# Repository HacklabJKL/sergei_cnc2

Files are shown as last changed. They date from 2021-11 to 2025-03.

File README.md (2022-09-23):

Sergei 2 CNC machine project
============================

This repository contains design files for Hacklab Jyväskylä's CNC machine project.
The machine is built out of existing linear assemblies that have been donated to us, and as such it is not readily reproducible. But some of the modules may be useful and in any case this repository contains information for future maintenance of the machine.

The machine design is a compromise between router and mill designs.
In general router-type CNC machines are more useful for our typical projects, as they have larger work area for flat stock.
But in the same time it would be desirable for the machine to be sturdy enough to cut mild steel at reasonable speeds.

The basic design is similar to fixed gantry routers or a portal milling machine.
X axis ballscrew assembly moves up and down on two Z axis columns.
Y axis moves the table.

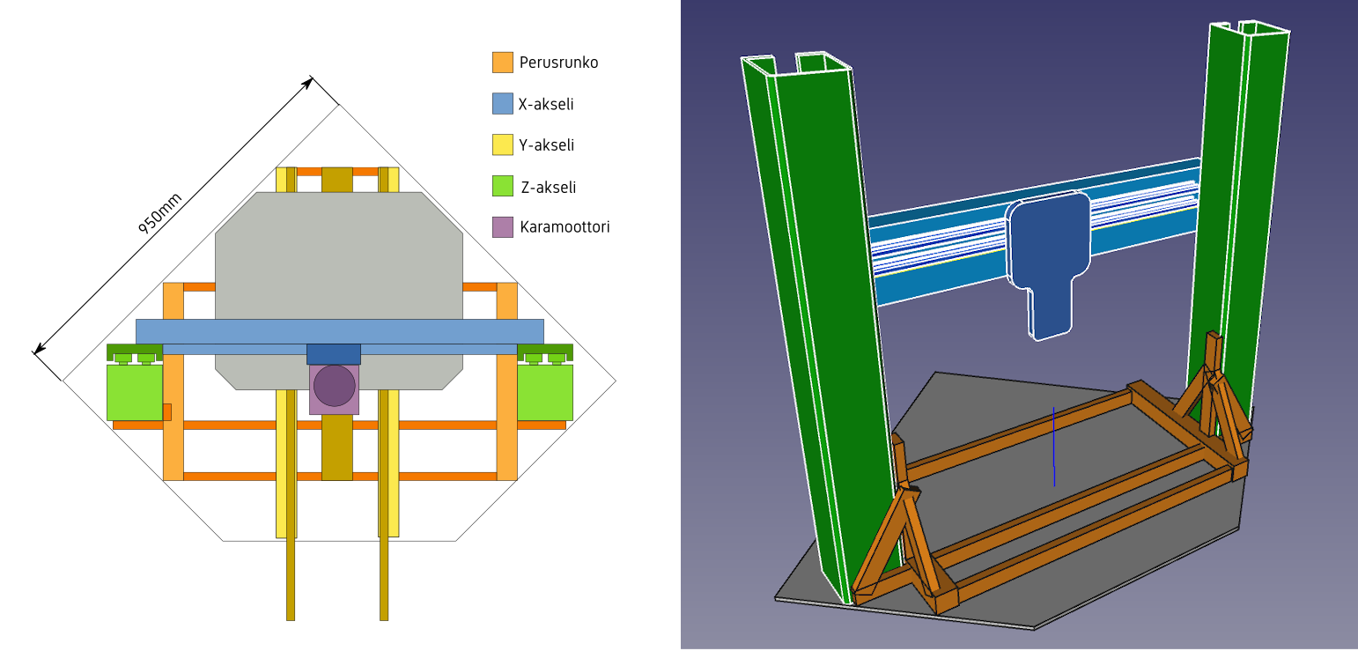
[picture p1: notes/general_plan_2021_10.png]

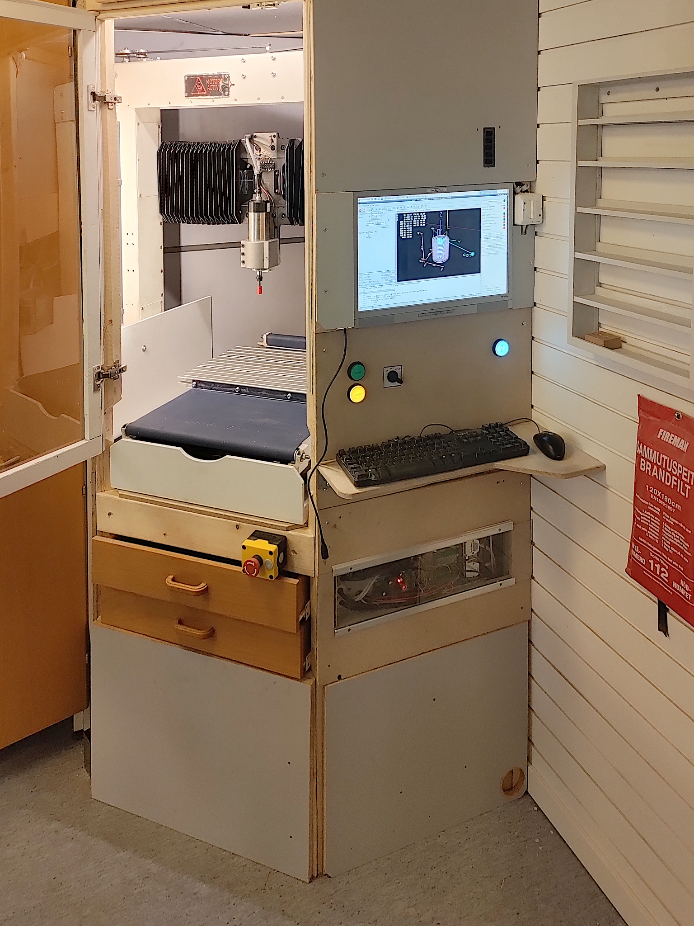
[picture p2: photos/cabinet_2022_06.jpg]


Documentation index
-------------------

* [Parts list](PARTS.md)
* [Wiring diagram](electronics/wiring/images/sergei2-wiring.pdf)
* [Usage instructions (wiki)](https://github.com/HacklabJKL/sergei_cnc2/wiki)

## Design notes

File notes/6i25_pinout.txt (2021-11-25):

2 ports of 17 IO pins each.

Port 1:
- 5 pins X: FWD/REV/FAULT/A/B
- 5 pins Y: FWD/REV/FAULT/A/B
- 5 pins Z: FWD/REV/FAULT/A/B
- HCURR output

Port 2:
- 5 pins A: FWD/REV/FAULT/A/B
- 2 pins 48V: ON/OK
- 1 pin SPINDLE_ON
- 1 pin TOOL_SENSOR
- 1 pin PROBE
- 3 pins X/Y/Z home

Port 1:
 1: X_FWD
 2: X_REV
 3: X_HOME
 4: X_A
 5: X_B
 6: Y_FWD
 7: Y_REV
 8: Y_HOME
 9: Y_A
10: Y_B
11: Z_FWD
12: Z_REV
13: Z_HOME
14: Z_A
15: Z_B
16: MOTOR_FAULT
17: MOTOR_HCURR

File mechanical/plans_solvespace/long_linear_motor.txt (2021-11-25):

2 pcs, 150 cm, 4x4 cm aluminum profile
table material?
Not quite long enough

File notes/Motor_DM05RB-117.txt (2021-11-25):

Specs: DC 24 V, 2000 RPM

12 cogging steps

DC resistance 5.5 ohms
Inductance 7 mH

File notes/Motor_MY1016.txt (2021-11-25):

Bought from eBay.
Rated 24V 300W 17A 2750 RPM.

DC Resistance 0.4 ohm
Inductance 0.5 mH

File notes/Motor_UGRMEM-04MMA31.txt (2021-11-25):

Speed testing:

10V:  600 RPM, 0.4 A
20V: 1340 RPM, 0.5 A
30V: 2110 RPM, 0.6 A
40V: 2890 RPM, 0.7 A
50V: 3660 RPM, 0.8 A

Kv constant 70 RPM/V
Kt constant 0.14 Nm/A

1 cm rise, 1:1 ratio:
=> 0.04 mm per pulse, 0.01 mm per encoder step
=> max speed 60 cm/sec
=> force with 5A drive is 440 N

Could use different ratio gearing, 1:2 or 1:4.

Mating connector: Molex 0003091032

DC resistance 5 ohms
Inductance 0.5 mH

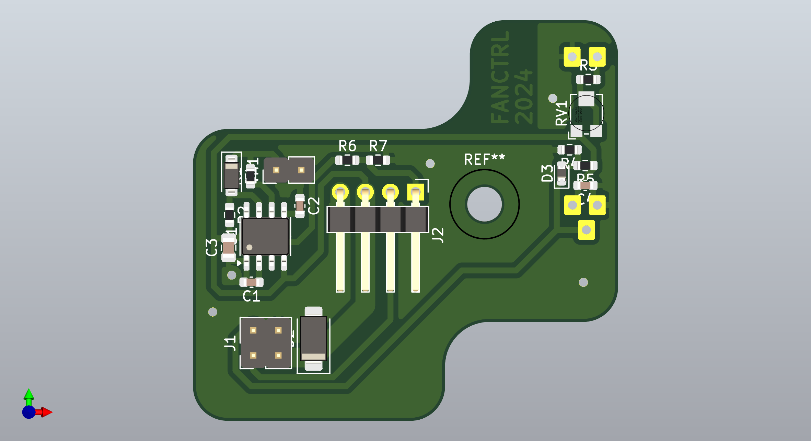
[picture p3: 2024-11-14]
electronics/spindle_fan_control/images/spindle_fan_control.png

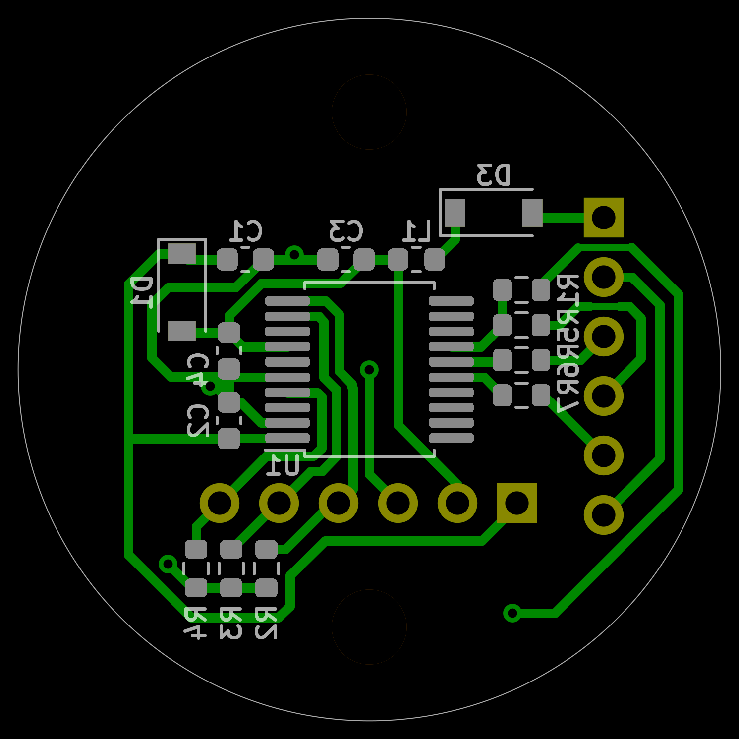
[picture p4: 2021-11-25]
electronics/motor_encoder/images/motor_encoder_bottom.png

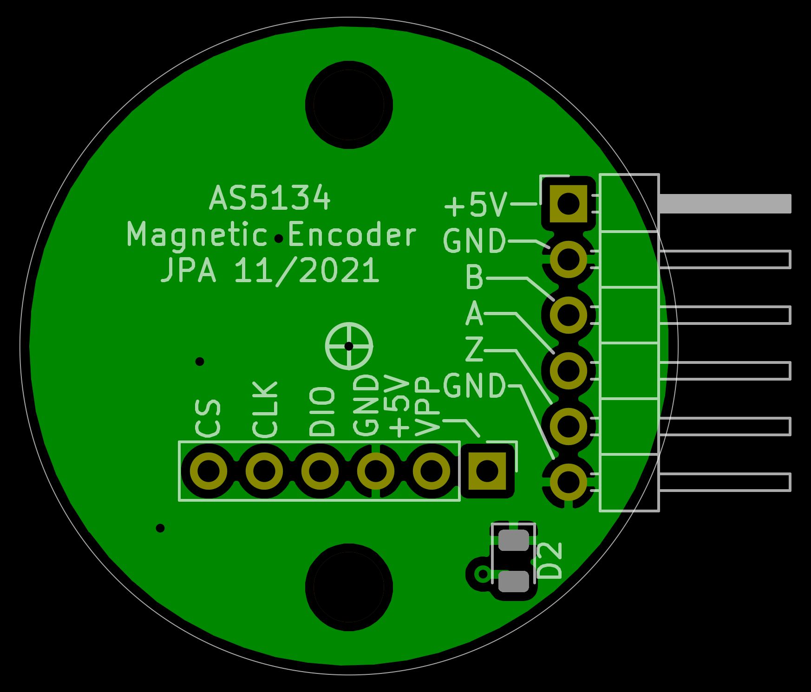
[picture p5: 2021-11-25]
electronics/motor_encoder/images/motor_encoder_top.png

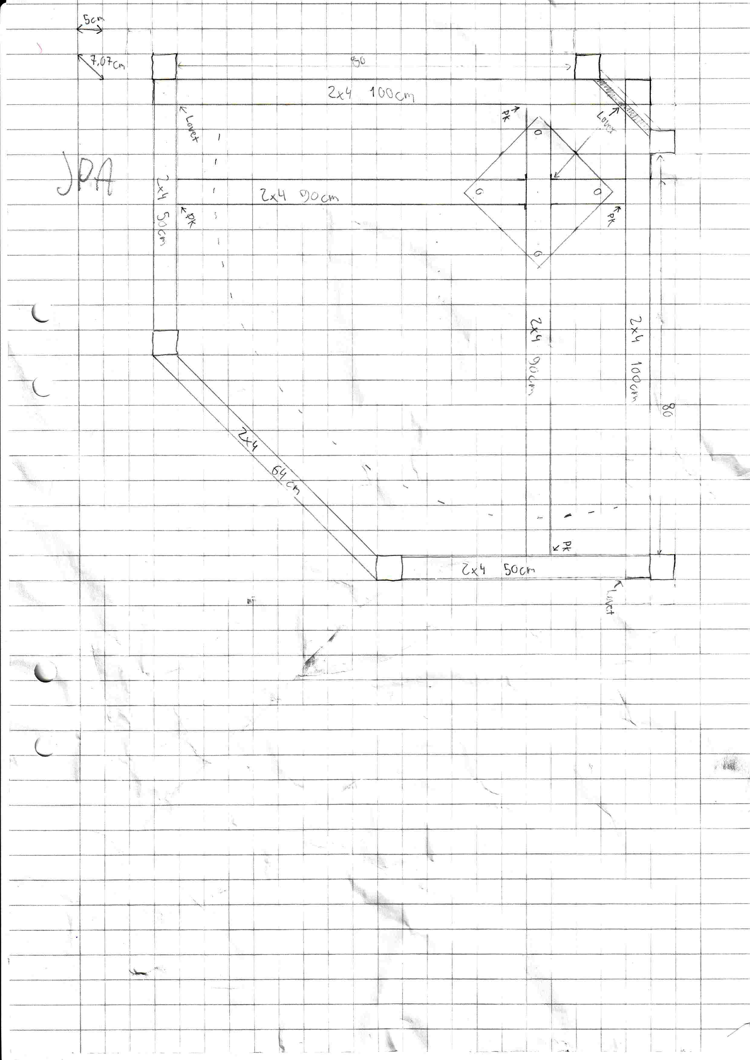
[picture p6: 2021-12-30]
notes/cabinet2.jpg

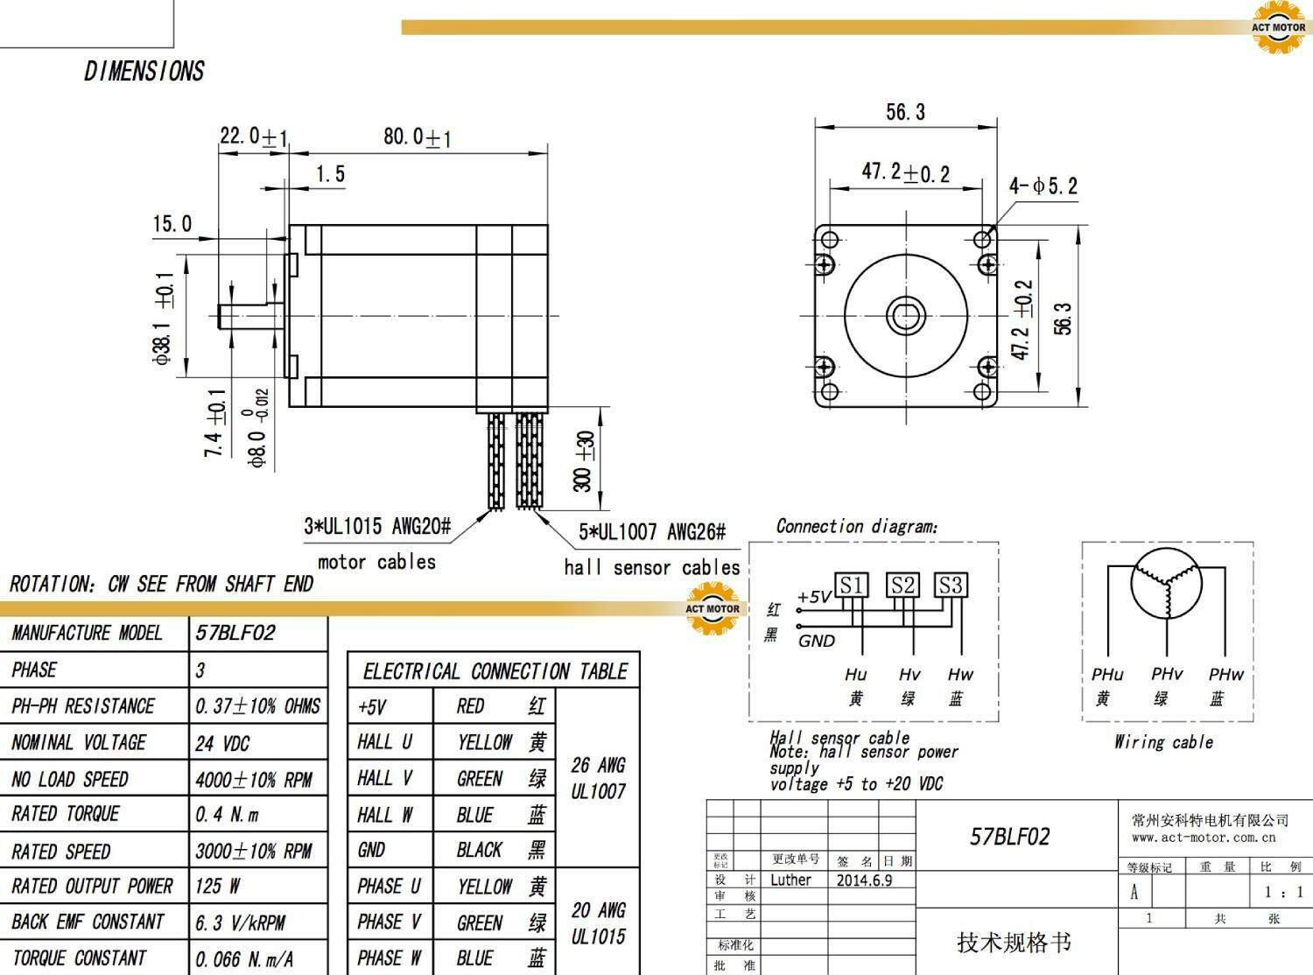
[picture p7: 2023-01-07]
datasheets/Motor_57BLF02.jpg

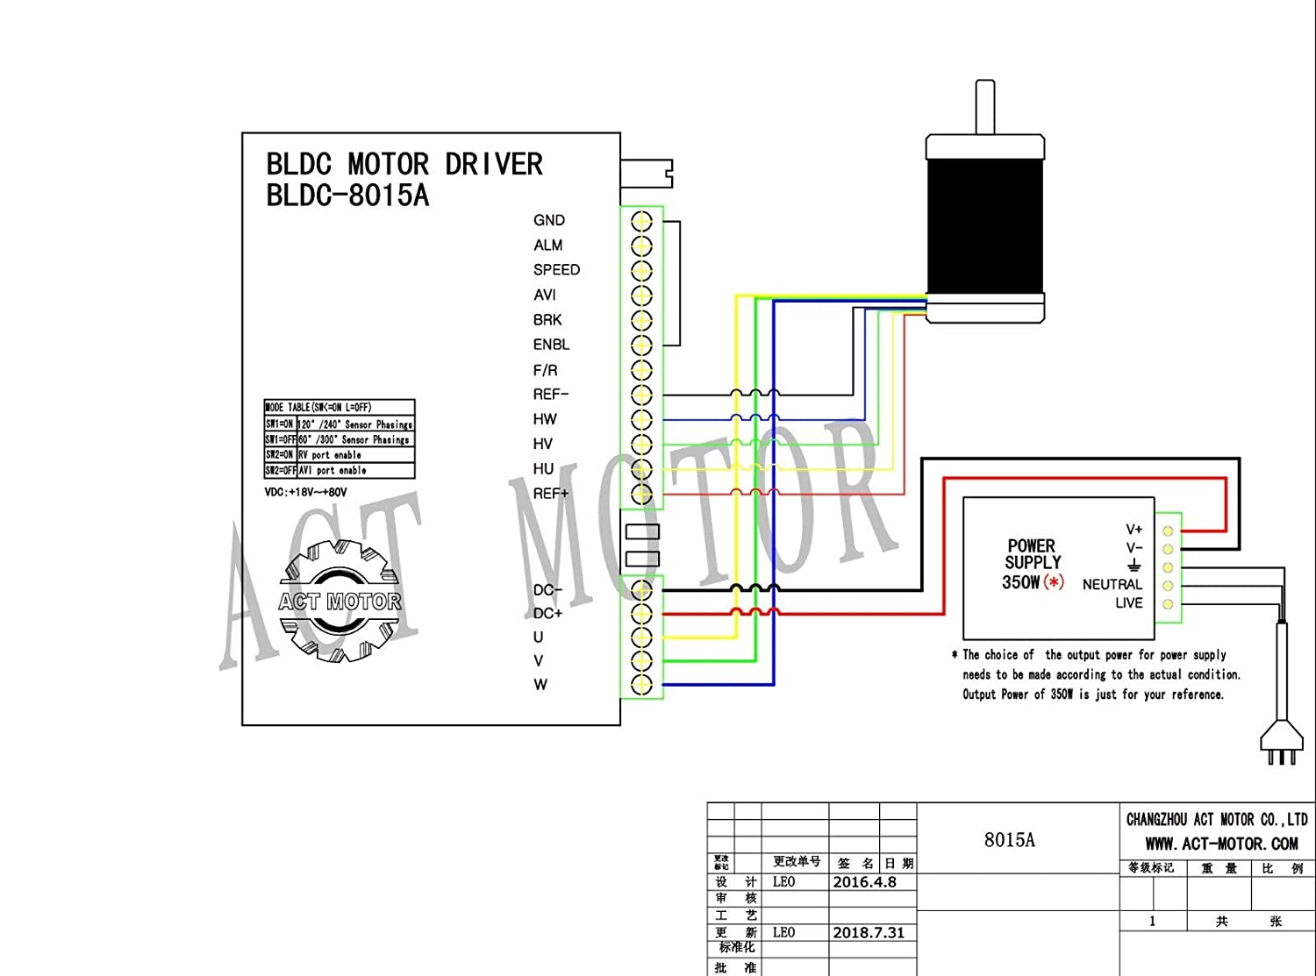
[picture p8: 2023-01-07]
datasheets/Motor_57BLF02_connections.jpg

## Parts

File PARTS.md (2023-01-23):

Sergei 2 CNC machine parts list
===============================

Machine body
------------

* 20x40 mm steel tubing
* 50x50 mm steel tubing
* M6 cap head screws
* Spray painted black

Bridge / X-axis
---------------

* Premade [1000 mm ballscrew linear assembly](mechanical/plans_solvespace/linear_assembly_1000mm.txt)
* Utopi DC [motor](notes/Motor_UGRMEM-04MMA31.txt) and [encoder](notes/Encoder_UTOPI_O25SD.txt)
* [DIY 48VDC motor driver](electronics/motor_driver/)
* Cable chain
* Mounted with M8 cap head screws
* Canvas dust shield, [DIY](http://essentialscrap.com/cnc2/dust_shields/)

Table / Y-axis
--------------

* Premade [760 mm ballscrew linear assembly](mechanical/plans_solvespace/linear_assembly_700mm.txt) for movement
* Utopi DC [motor](notes/Motor_UGRMEM-04MMA31.txt) and [encoder](notes/Encoder_UTOPI_O25SD.txt)
* [DIY 48VDC motor driver](electronics/motor_driver/)
* Dual linear rails for table support
* [Aluminum extrusion 30x120 I-type](https://www.dold-mechatronik.de/Aluminum-profile-30x120L-I-type-groove-6) for T-slot table

Columns / Z-axis
----------------

* Two premade [1100 mm linear assemblies](mechanical/plans_solvespace/linear_assembly_1100mm.txt)
* Trapezoidal screws TR12x3 installed inside each column
* Top end: 2x angular contact ball bearings 3201-2RS
* Bottom end (trapezoidal screw tensioner): 2x single row ball bearings 6201-2RS
* Cable chain inside columns
* Belt drive from a central motor:
  * 2x GT2 belt, 6 mm wide:
    * 1140-1150 mm loop on left side
    * 1130-1140 mm loop on right side
  * 2x 100 tooth pulleys, 12 mm bore
  * 1x dual 20T pulley, 8 mm bore
  * 2x belt tensioners
* [Motor 57BLF02](datasheets/Motor_57BLF02.jpg)
* [Motor driver BD15A8](datasheets/bd15a8.pdf)
* [Encoder AS5134](electronics/motor_encoder)

Spindle
-------

* [Vevor 0.8kW Air-cooled ER11 spindle](https://eur.vevor.com/spindle-motor-c_10130/vevor-0-8kw-er11-air-cooled-spindle-motor-24000rpm-for-milling-engraving-machine-p_010636027589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{en}_{EU}_{orderDelivery}_{2022-04-25%2017:21:27})
* [Vevor 1.5kW VFD](https://eur.vevor.com/variable-frequency-drives-c_10745/vevor-2hp-1-5kw-vfd-variable-frequency-drive-220v-inverter-soundl-solutions-p_010276894883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{en}_{EU}_{orderDelivery}_{2022-04-24%2019:21:47}) [manual](datasheets/Vevor_A2_8015_VFD_Manual_v1.8.pdf)
* [65 mm spindle motor clamp](https://www.ebay.com/itm/293600909919)
* 50°C overtemperature switch
* [NICEYRIG rail](https://www.ebay.com/itm/293185219621) for mounting dust collection & other extra tools

Coolant supply
--------------

* 2x 4 mm hose routed through cable chains in right side Z column and X axis to the spindle mount.
* [24V peristaltic pump](https://www.ebay.com/itm/274481580980)

Cabinet
-------

* 48x48 mm vertical wood beams
* 48x98 mm horizontal wood beams
* Plywood base for the machine
* Originally designed for robot hand project, original plans: [1](notes/cabinet1.jpg) [2](notes/cabinet2.jpg)

Control PC
----------

* Dell OptiPlex 990/0D6H9T, 8 GB RAM, 120 GB SSD
* [Mesa 6i25 FPGA card](http://store.mesanet.com/index.php?route=product/product&product_id=58)
* Novation Nocturn USB pad for manual control

Control electronics
-------------------
* 48 VDC 2 kW power supply for axis motors
* Operating mode selection switch: [GX1653U](https://www.tme.eu/en/details/gx1653u/cam-switches/lovato-electric/) or similar
* Emergency stop switch
* [Power control board](electronics/power_control_pcb/images/power_control_pcb.pdf)
* [Wiring diagram](electronics/wiring/images/sergei2-wiring.pdf)

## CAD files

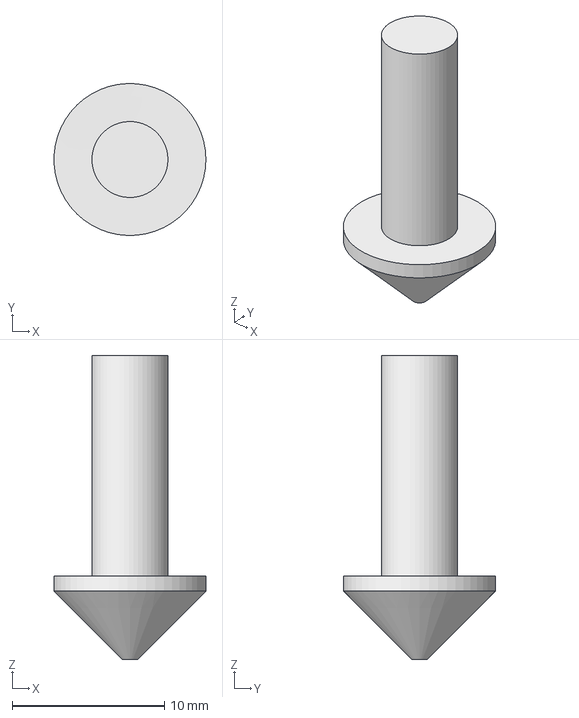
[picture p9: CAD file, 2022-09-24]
CAM_configs/FreeCAD/Toolbits/Shape/v-bit.fcstd
9.99 x 10.00 x 20.0 mm

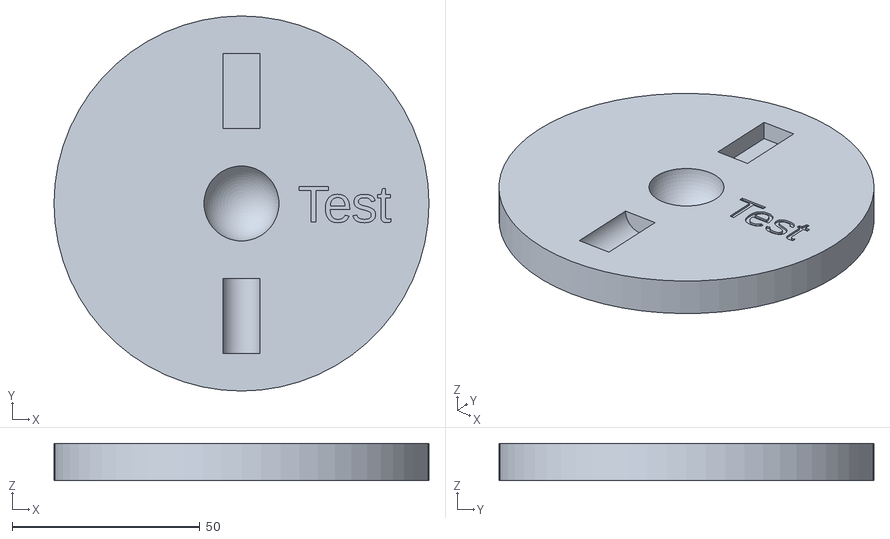
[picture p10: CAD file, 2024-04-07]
CAM_configs/KiriMoto/esimerkkikappale/esimerkkikappale.stl
100.0 x 100.0 x 10.0

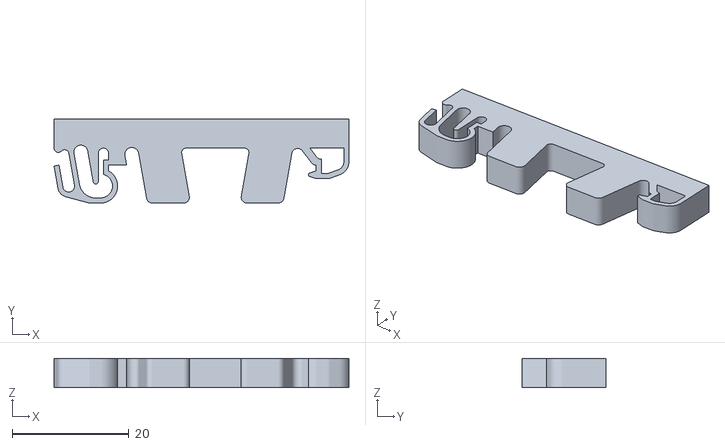
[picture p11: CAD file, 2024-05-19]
mechanical/din_rail_mount/DINrail_Clip-Body.stl
50.5 x 14.4 x 5.00

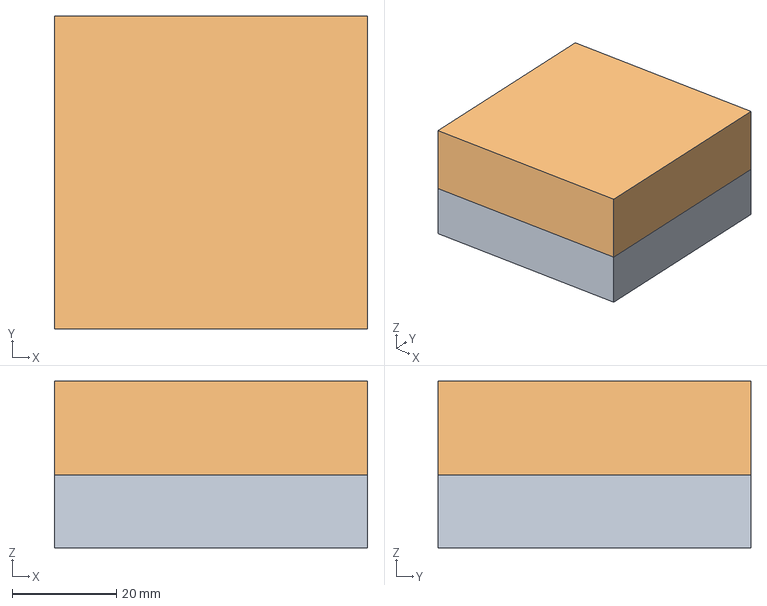
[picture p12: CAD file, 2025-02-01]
mechanical/misc_parts/spindle_fan_magnetmount.FCStd
60.0 x 60.0 x 32.0 mm
Stock
Stock002

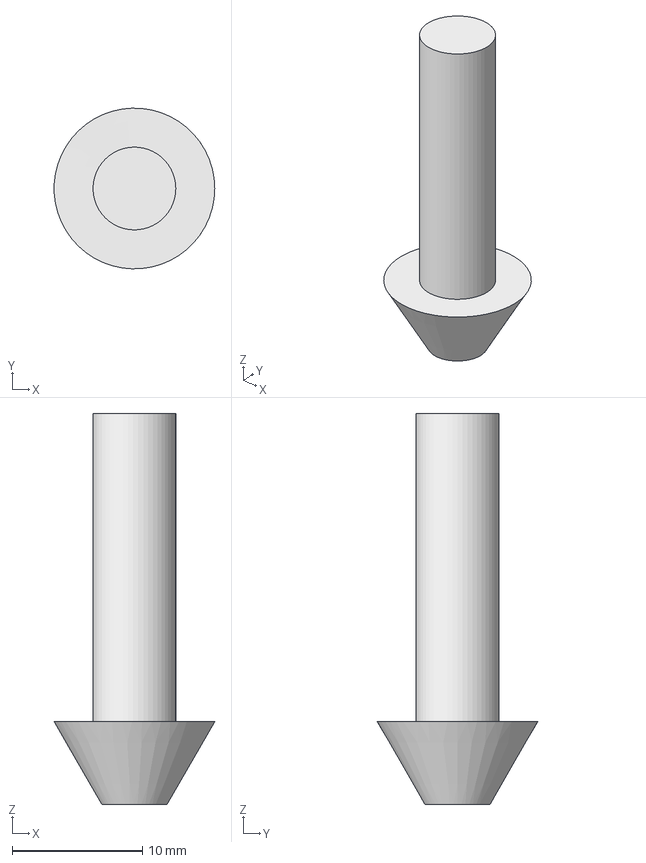
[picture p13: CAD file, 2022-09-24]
CAM_configs/FreeCAD/Toolbits/Shape/chamfer.fcstd
12.3 x 12.3 x 30.0 mm

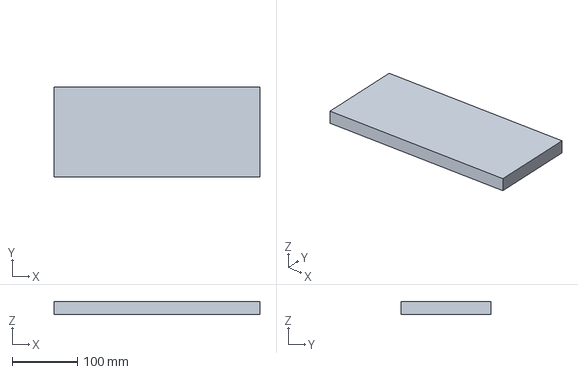
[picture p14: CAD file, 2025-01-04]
mechanical/misc_parts/z_carriage_mount.FCStd
315.0 x 138.0 x 20.0 mm

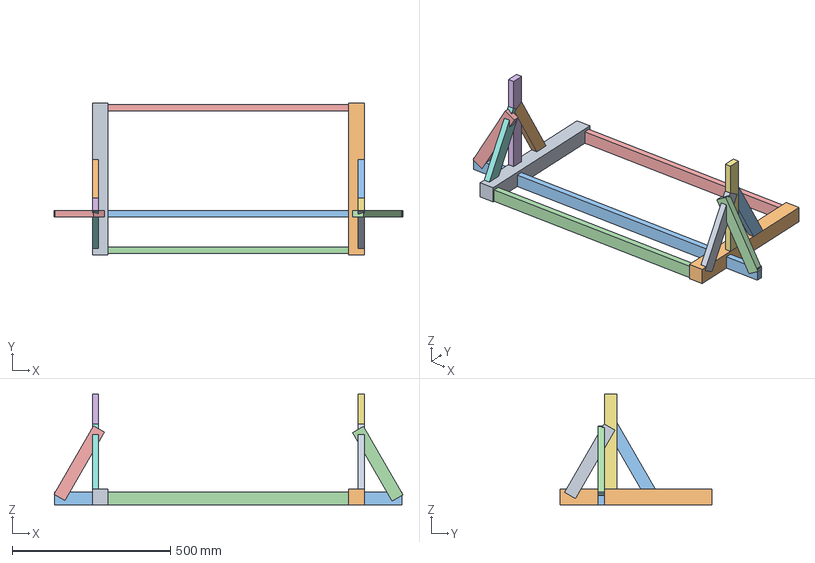
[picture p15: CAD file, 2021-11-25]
mechanical/plans_freecad/body.FCStd
1104.0 x 480.0 x 350.0 mm
y_base1
y_base2
x_base
x_span1
x_span2
z_support1
z_support2
diagonal1
diagonal2
diagonal3
diagonal4
diagonal5
diagonal6

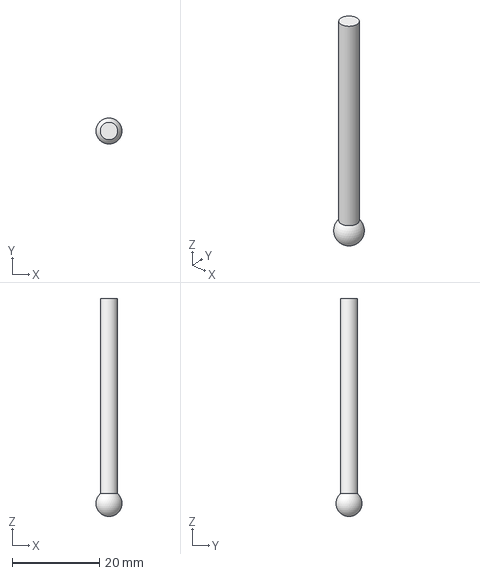
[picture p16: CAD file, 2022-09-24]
CAM_configs/FreeCAD/Toolbits/Shape/probe.fcstd
5.99 x 5.98 x 50.0 mm

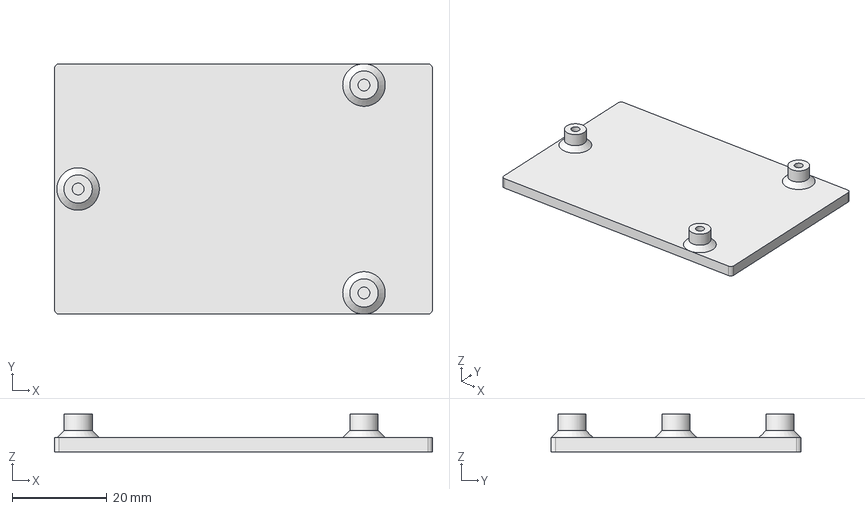
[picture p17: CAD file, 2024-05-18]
mechanical/din_rail_mount/Mount_DB25_G2.FCStd
80.0 x 53.0 x 8.00 mm

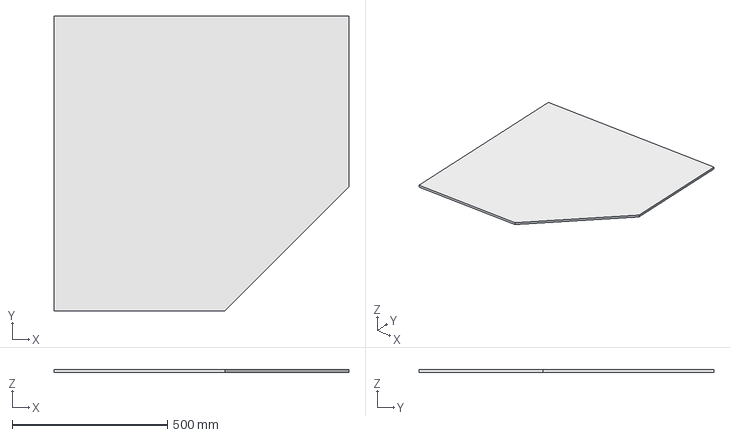
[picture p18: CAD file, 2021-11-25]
mechanical/plans_freecad/plywood_base.FCStd
950.0 x 950.0 x 10.0 mm

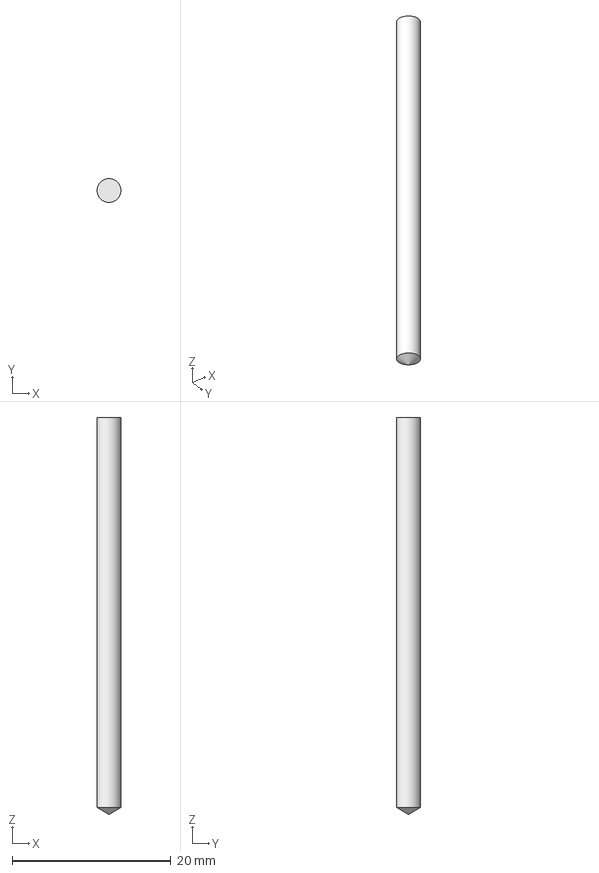
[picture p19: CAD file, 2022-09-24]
CAM_configs/FreeCAD/Toolbits/Shape/drill.fcstd
3.00 x 3.00 x 50.0 mm

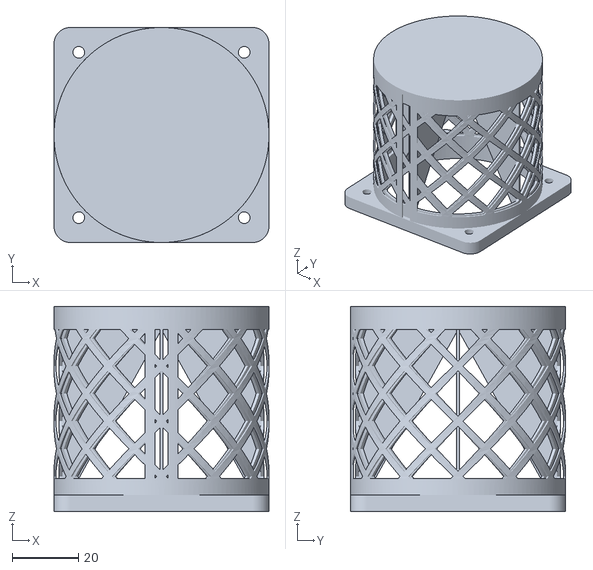
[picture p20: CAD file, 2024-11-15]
mechanical/misc_parts/spindle_fan-IntakeFilter.stl
65.0 x 65.0 x 62.0

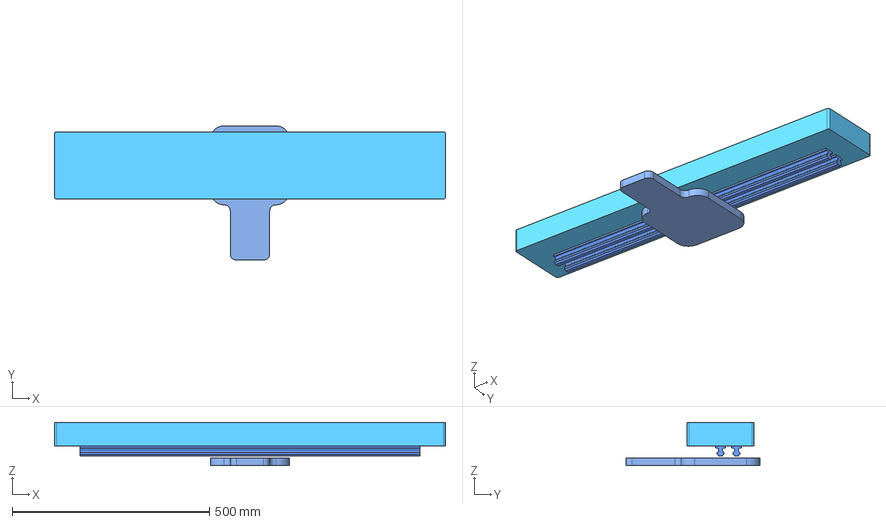
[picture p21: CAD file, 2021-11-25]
mechanical/plans_freecad/linear_860.FCStd
990.0 x 340.0 x 110.0 mm

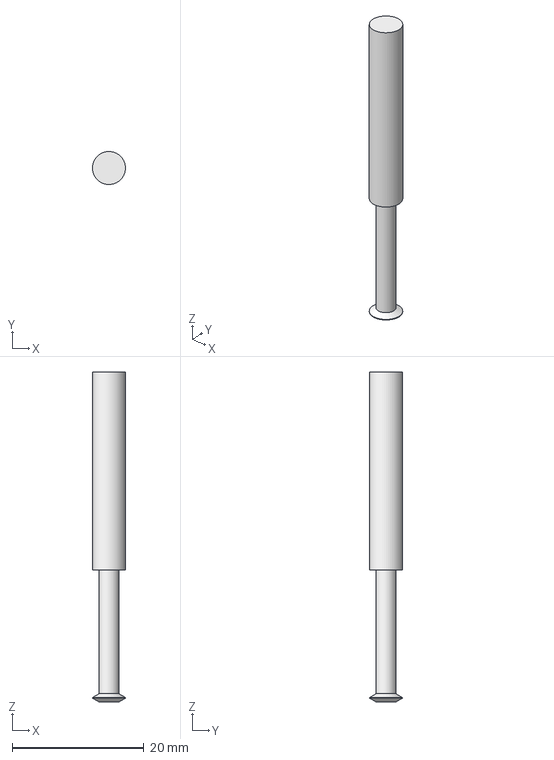
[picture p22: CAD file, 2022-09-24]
CAM_configs/FreeCAD/Toolbits/Shape/thread-mill.fcstd
5.00 x 5.00 x 50.0 mm

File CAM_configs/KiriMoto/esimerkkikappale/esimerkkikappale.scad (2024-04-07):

$fn = 60;

difference()
{
    cylinder(10, 50, 50);

    translate([0,0,10]) sphere(10);

    translate([15,-5,9.5]) linear_extrude(1) text("Test");
    
    translate([-5,20,5]) cube([10, 20, 10]);
    
    translate([0,-40,10]) rotate([-90,0,0]) cylinder(20, 5, 5);
}

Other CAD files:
mechanical/plans_freecad/assembly.FCStd
mechanical/din_rail_mount/DINrail_Clip.fcstd
mechanical/din_rail_mount/Mount_DB25_G2-PartBody.stl
mechanical/din_rail_mount/Mount_Power_control_PCB.FCStd
CAM_configs/FreeCAD/Toolbits/Shape/ballend.fcstd
CAM_configs/FreeCAD/Toolbits/Shape/bullnose.fcstd
CAM_configs/FreeCAD/Toolbits/Shape/endmill.fcstd
CAM_configs/FreeCAD/Toolbits/Shape/slittingsaw.fcstd
mechanical/din_rail_mount/Mount_Buck-Part.stl
mechanical/din_rail_mount/Mount_Buck.FCStd
mechanical/din_rail_mount/Mount_Power_control_PCB-Part.stl
mechanical/misc_parts/camera_holder.stl
mechanical/misc_parts/holddown_clamp.FCStd
mechanical/misc_parts/t_nut.FCStd
mechanical/misc_parts/toe_clamp.FCStd
mechanical/plans_freecad/linear_1100.FCStd
mechanical/plans_freecad/linear_760.FCStd
mechanical/plans_freecad/test.FCStd

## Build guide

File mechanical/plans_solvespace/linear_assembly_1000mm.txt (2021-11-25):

Kuularuuvi 14mm, 1cm nousu
1:1 välitys
Optical encoder UTOPI-O25SD, 250pulses/rev
Minertia motor, UGRMEM-04MMA31
UTOPI-025SD

=> 0.04 mm/pulse

Cart extension 150 mm from lower edge

Fits 1100 mm carts sideways at 910 mm distance between inner faces

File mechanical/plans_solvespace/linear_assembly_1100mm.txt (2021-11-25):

Use as machine body?

1105mm length, bolt rails vertically at ends
1cm thickness + 4cm cart
Remaining width 1005 mm
Plenty for attaching linear rail 1000 mm in between.

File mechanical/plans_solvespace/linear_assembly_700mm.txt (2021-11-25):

Length total 760, rails 685, movement 590
Depth without motor 60mm to screw, 75mm to bearing block, 100mm to cart attachment

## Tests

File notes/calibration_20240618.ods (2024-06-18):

Active calibration
C0 | 0.999990 | C_xx
C1 | 0.000000 | C_xy
C2 | -0.005510 | C_xz
C3 | 0.000000 | C_yx
C4 | 0.999800 | C_yy
C5 | -0.000870 | C_yz
C6 | 0.000000 | C_zx
C7 | 0.000300 | C_zy
C8 | 1.000000 | C_zz
X / Y Scale
Y axis top edge | 82.258333 | mm
Y axis bottom edge | -73.398667 | mm
Y axis measured length | 155.657000 | 155.625869
X axis left edge | -108.750500 | mm
X axis right edge | 46.955500 | mm
X axis measured length | 155.706000 | 155.704443
New C4 | 0.999495
Verify X length | 100.226000 | mm
Reference (caliper) | 100.240000 | mm
Verify error | 0.000140 | ratio
X / Y Squaring
Left edge angle | -0.026600 | deg
Bottom edge angle | -0.041500 | deg
Angle | 90.014900 | deg
Right edge angle | 0.030500 | deg
Bottom edge angle | -0.027000 | deg
Angle | 89.942500 | deg
Reference angle | 89.978700 | deg
Skew | 0.036200 | deg
New C1 | -0.000631 | rad
Verify right | -0.008000 | deg
Verify bottom | -0.028000 | deg
Angle | 89.980000 | deg
Verify error | 0.001300 | deg
X / spindle squaring
Z difference | 0.110000 | mm
X difference | 182.590000 | mm
New C6 | 0.000602
Verify Z difference | 0.010000 | mm
Y / spindle squaring
Z difference | 0.220000 | mm
Y difference | 184.240000 | mm
New C7 | -0.000894
Verify Z difference | 0.015000 | mm
Z / spindle squaring in X
X difference | 0.140000 | mm
Z difference | 73.180000 | mm
New C2 | -0.003597
Verify X difference | 0.020000 | mm
Z / spindle squaring in Y
Y difference | 0.150000 | mm
Z difference | 66.880000 | mm
New C5 | 0.001373
Verify Y difference | 0.000000 | mm
Camera
X difference | -0.230000 | mm
Y difference | -0.055000 | mm
Backlash
Z backlash (0.1 mm move) | 0.010000 | mm
X backlash (0.1 mm move) | 0.015000 | mm
Y backlash (0.1 mm move) | 0.050000 | mm

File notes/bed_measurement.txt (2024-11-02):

# [MATRIXKINS]
# Mechanical alignment calibration
# See hal_components/matrixkins.comp for calibration instructions.
#  | X_joint |   | C0 C1 C2 |   | X_axis |
#  | Y_joint | = | C3 C4 C5 | * | Y_axis |
#  | Z_joint |   | C6 C7 C8 |   | Z_axis |
# C0 =  0.99999
# C1 = -0.00063
# C2 = -0.00360
# C3 =  0.0    
# C4 =  0.99950
# C5 =  0.00137
# C6 =  0.00060
# C7 = -0.00089
# C8 =  1.0

12:37:28: ZMinus result X -274.263 Y 151.822 Z 13.743
12:37:38: ZMinus result X -274.265 Y 147.785 Z 13.713 Angle -0.429 deg
12:37:44: ZMinus result X -274.265 Y 155.859 Z 13.753 Angle 0.288 deg
12:37:50: ZMinus result X -274.268 Y 151.822 Z 13.743 Angle -0.146 deg
12:37:59: ZMinus result X -260.862 Y 151.827 Z 13.747 Angle 0.016 deg
12:38:06: ZMinus result X -237.397 Y 151.827 Z 13.754 Angle 0.019 deg
12:38:13: ZMinus result X -177.067 Y 151.827 Z 13.773 Angle 0.018 deg
12:38:24: ZMinus result X -131.496 Y 151.827 Z 13.809 Angle 0.045 deg
12:38:31: ZMinus result X -83.230 Y 151.827 Z 13.855 Angle 0.055 deg
12:38:38: ZMinus result X -22.900 Y 151.827 Z 13.874 Angle 0.018 deg
12:38:44: ZMinus result X 30.736 Y 151.827 Z 13.858 Angle -0.017 deg
12:38:50: ZMinus result X 81.036 Y 151.827 Z 13.813 Angle -0.051 deg
12:38:56: ZMinus result X 134.666 Y 151.827 Z 13.726 Angle -0.093 deg
12:39:07: ZMinus result X 164.837 Y 151.827 Z 13.671 Angle -0.104 deg
12:39:13: ZMinus result X 209.767 Y 151.827 Z 13.588 Angle -0.107 deg
12:39:23: ZMinus result X 246.637 Y 151.827 Z 13.510 Angle -0.120 deg
12:39:37: ZMinus result X 281.467 Y 151.828 Z 13.431 Angle -0.130 deg
12:39:50: ZMinus result X 281.469 Y 162.558 Z 13.412 Angle -0.100 deg
12:39:54: ZMinus result X 281.466 Y 158.526 Z 13.429 Angle 0.233 deg
12:39:58: ZMinus result X 281.464 Y 154.524 Z 13.437 Angle 0.116 deg
12:40:02: ZMinus result X 281.466 Y 150.492 Z 13.418 Angle -0.264 deg
12:40:07: ZMinus result X 281.468 Y 146.460 Z 13.383 Angle -0.501 deg
12:40:24: ZMinus result X 281.469 Y 125.024 Z 13.251 Angle -0.354 deg
12:40:29: ZMinus result X 281.469 Y 92.858 Z 13.314 Angle 0.112 deg
12:40:34: ZMinus result X 281.469 Y 68.061 Z 13.282 Angle -0.074 deg
12:40:41: ZMinus result X 281.466 Y 72.058 Z 13.299 Angle 0.242 deg
12:40:45: ZMinus result X 281.469 Y 52.593 Z 13.235 Angle -0.188 deg
12:40:49: ZMinus result X 281.467 Y 56.625 Z 13.350 Angle 1.637 deg
12:40:54: ZMinus result X 281.471 Y 40.557 Z 13.184 Angle -0.592 deg
12:40:59: ZMinus result X 281.469 Y 30.527 Z 13.175 Angle -0.051 deg
12:41:04: ZMinus result X 281.471 Y 3.024 Z 12.969 Angle -0.429 deg
12:41:08: ZMinus result X 281.468 Y -27.141 Z 13.065 Angle 0.183 deg
12:41:13: ZMinus result X 281.470 Y -48.607 Z 13.141 Angle 0.203 deg
12:41:18: ZMinus result X 281.469 Y -66.011 Z 13.181 Angle 0.130 deg
12:41:22: ZMinus result X 281.469 Y -81.444 Z 13.092 Angle -0.329 deg
12:41:26: ZMinus result X 281.471 Y -116.976 Z 12.912 Angle -0.290 deg
12:41:31: ZMinus result X 281.473 Y -145.806 Z 12.946 Angle 0.068 deg
12:41:46: ZMinus result X 281.466 Y -116.676 Z 12.911 Angle -0.070 deg
12:41:50: ZMinus result X 261.336 Y -116.676 Z 12.916 Angle 0.015 deg
12:41:54: ZMinus result X 229.800 Y -116.676 Z 12.923 Angle 0.013 deg
12:42:00: ZMinus result X 199.635 Y -116.676 Z 12.923 Angle -0.000 deg
12:42:05: ZMinus result X 166.100 Y -116.671 Z 12.930 Angle 0.012 deg
12:42:10: ZMinus result X 129.204 Y -116.676 Z 12.949 Angle 0.029 deg
12:42:16: ZMinus result X 88.969 Y -116.676 Z 12.976 Angle 0.039 deg
12:42:24: ZMinus result X 35.339 Y -116.676 Z 12.993 Angle 0.018 deg
12:42:30: ZMinus result X -13.597 Y -116.676 Z 13.014 Angle 0.025 deg
12:42:50: ZMinus result X -52.462 Y -116.676 Z 13.039 Angle 0.037 deg
12:42:55: ZMinus result X -96.032 Y -116.676 Z 13.085 Angle 0.061 deg
12:42:59: ZMinus result X -137.598 Y -116.676 Z 13.125 Angle 0.055 deg
12:43:05: ZMinus result X -185.863 Y -116.676 Z 13.201 Angle 0.090 deg
12:43:10: ZMinus result X -242.828 Y -116.672 Z 13.277 Angle 0.076 deg
12:43:21: ZMinus result X -262.963 Y -116.677 Z 13.287 Angle 0.030 deg
12:43:33: ZMinus result X -262.967 Y 4.659 Z 13.320 Angle 0.016 deg
12:43:37: ZMinus result X -237.497 Y 4.659 Z 13.308 Angle -0.027 deg
12:43:42: ZMinus result X -197.261 Y 4.659 Z 13.291 Angle -0.025 deg
12:43:47: ZMinus result X -168.431 Y 4.659 Z 13.274 Angle -0.034 deg
12:43:51: ZMinus result X -139.596 Y 4.664 Z 13.256 Angle -0.034 deg
12:43:56: ZMinus result X -110.766 Y 4.659 Z 13.229 Angle -0.054 deg
12:44:01: ZMinus result X -70.530 Y 4.659 Z 13.185 Angle -0.063 deg
12:44:05: ZMinus result X -36.965 Y 4.664 Z 13.181 Angle -0.006 deg
12:44:11: ZMinus result X 24.036 Y 4.659 Z 13.160 Angle -0.020 deg
12:44:16: ZMinus result X 57.536 Y 4.659 Z 13.131 Angle -0.049 deg
12:44:20: ZMinus result X 91.071 Y 4.659 Z 13.108 Angle -0.040 deg
12:44:25: ZMinus result X 124.601 Y 4.659 Z 13.088 Angle -0.034 deg
12:44:30: ZMinus result X 163.467 Y 4.659 Z 13.043 Angle -0.066 deg
12:44:35: ZMinus result X 195.637 Y 4.665 Z 13.005 Angle -0.067 deg
12:44:40: ZMinus result X 234.167 Y 4.660 Z 12.989 Angle -0.024 deg
12:44:45: ZMinus result X 277.702 Y 4.660 Z 12.968 Angle -0.028 deg
12:45:28: ZMinus result X 277.699 Y -25.511 Z 13.056 Angle 0.167 deg
12:45:33: ZMinus result X 217.368 Y -25.506 Z 13.069 Angle 0.012 deg
12:45:45: ZMinus result X 143.633 Y -25.506 Z 13.151 Angle 0.064 deg
12:46:10: ZMinus result X 110.828 Y -25.506 Z 13.186 Angle 0.061 deg
12:46:15: ZMinus result X 62.562 Y -25.506 Z 13.216 Angle 0.036 deg
12:46:20: ZMinus result X 31.027 Y -25.506 Z 13.244 Angle 0.050 deg
12:46:25: ZMinus result X -44.039 Y -25.506 Z 13.262 Angle 0.014 deg
12:46:30: ZMinus result X -88.939 Y -25.506 Z 13.296 Angle 0.043 deg
12:46:35: ZMinus result X -147.939 Y -25.506 Z 13.358 Angle 0.060 deg
12:46:40: ZMinus result X -196.875 Y -25.506 Z 13.385 Angle 0.032 deg
12:46:45: ZMinus result X -240.470 Y -25.506 Z 13.417 Angle 0.041 deg
12:46:50: ZMinus result X -270.640 Y -25.506 Z 13.425 Angle 0.015 deg

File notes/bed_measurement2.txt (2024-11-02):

# C0 =  0.99999
# C1 = -0.00063
# C2 = -0.00360
# C3 =  0.0    
# C4 =  0.99950
# C5 =  0.00137
# C6 =  0.00004
# C7 =  0.001
# C8 =  1.0

12:58:39: ZMinus result X -280.371 Y -25.511 Z 13.322 Angle 0.022 deg
12:58:45: ZMinus result X -216.665 Y -25.506 Z 13.323 Angle 0.001 deg
12:58:50: ZMinus result X -152.970 Y -25.506 Z 13.323 Angle 0.001 deg
12:58:56: ZMinus result X -82.569 Y -25.506 Z 13.290 Angle -0.027 deg
12:59:02: ZMinus result X -10.138 Y -25.506 Z 13.311 Angle 0.016 deg
12:59:07: ZMinus result X 46.862 Y -25.506 Z 13.297 Angle -0.014 deg
12:59:13: ZMinus result X 105.863 Y -25.506 Z 13.288 Angle -0.009 deg
12:59:19: ZMinus result X 162.828 Y -25.506 Z 13.269 Angle -0.019 deg
12:59:25: ZMinus result X 246.664 Y -25.506 Z 13.264 Angle -0.003 deg
12:59:31: ZMinus result X 291.560 Y -25.506 Z 13.247 Angle -0.021 deg
12:59:46: ZMinus result X 83.730 Y -149.543 Z 13.305 Angle 0.014 deg
12:59:50: ZMinus result X 83.725 Y -116.011 Z 13.243 Angle -0.106 deg
12:59:55: ZMinus result X 83.726 Y -83.840 Z 13.407 Angle 0.293 deg
12:59:59: ZMinus result X 83.725 Y -46.081 Z 13.396 Angle -0.017 deg
13:00:03: ZMinus result X 83.728 Y -24.616 Z 13.290 Angle -0.284 deg
13:00:08: ZMinus result X 83.727 Y 5.555 Z 13.143 Angle -0.279 deg
13:00:20: ZMinus result X 83.727 Y 5.555 Z 13.148
13:00:25: ZMinus result X 83.727 Y 36.385 Z 13.345 Angle 0.367 deg
13:00:31: ZMinus result X 83.729 Y 94.054 Z 13.508 Angle 0.161 deg
13:00:37: ZMinus result X 83.728 Y 125.855 Z 13.406 Angle -0.183 deg
13:00:41: ZMinus result X 83.729 Y 157.355 Z 13.568 Angle 0.294 deg

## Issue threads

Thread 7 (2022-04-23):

Terän pituusanturi

PetteriAimonen, 2022-04-23:
Terän pituuden mittaamiseen automaattisesti tarvitaan anturi, "tool length sensor". Hyvä olisi että anturi toimisi myös ohuille 0.5mm piirilevyporille, eli sen aktivointivoiman pitää olla pieni tai sitten sen pitää toimia optisesti.

- [x] Anturin hankinta / rakentaminen
- [x] Anturin sijoituspaikan valinta niin ettei tule jyrsinnän tielle
- [x] LinuxCNC konffaus

PetteriAimonen, 2022-08-08:
Konffattu ja periaatteessa toimii, mutta tarkkuus jättää toivomisen varaa.

PetteriAimonen, 2023-06-20:
Sijoiteltu paremmin ja tukevammin.

Closed 2023-06-20.

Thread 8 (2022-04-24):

Karamoottorin johdotus

PetteriAimonen, 2022-04-24:
Tilattu [karamoottori](https://eur.vevor.com/spindle-motor-c_10130/vevor-0-8kw-er11-air-cooled-spindle-motor-24000rpm-for-milling-engraving-machine-p_010636027589) ja [taajuusmuuntaja](https://eur.vevor.com/variable-frequency-drives-c_10745/vevor-2hp-1-5kw-vfd-variable-frequency-drive-220v-inverter-soundl-solutions-p_010276894883).

Taajuusmuuntaja tulee muiden virtalähteiden kanssa alakaappiin. Siitä kaapelointi karamoottorille.

- [X] Kaapeliketjun asennus Z-akselille
- [x] Kaapeliketjun asennus X-akselille
- [x] Kaapelien pujotus ja liittimien asennus

Closed 2022-05-07.

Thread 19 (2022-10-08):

G64 pyöristysmoodi meni mystisesti päälle

PetteriAimonen, 2022-10-08:
Oletuksena LinuxCNC on konffattu `G64 P0.01 Q0.01` moodiin, jossa jyrsintäpolussa olevat nurkat mennään korkeintaan `0.01mm` virheellä.

Tänään kesken jyrsinnän moodiksi kuitenkin jotenkin vaihtui `G64` ilman maksimitoleranssia, jolloin kulmat pyöristyvät melkoisesti liikaa.

Tiedostoissa ei näkynyt G64-käskyä.

Olisi hyvä jos maksimipyöristymisen saisi rajoitettua tai jos edes nykyisen tilanteen saisi näkyville.

PetteriAimonen, 2022-10-08:
Johtuu tästä bugista: https://github.com/LinuxCNC/linuxcnc/issues/177

Closed 2022-10-22.

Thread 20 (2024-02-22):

Teräksen jyrsintä / matalien kierrosten vääntö

PetteriAimonen, 2024-02-22:
Tällä hetkellä karamoottori ei jaksa vääntää juurikaan alle 8000 RPM. Tämä on teräkselle turhan nopea kierrosluku ja aiheuttaa herkästi terän ylikuumenemista. Vektoriohjauksella oleva VFD lisäisi vääntöä, mutta pitää varmistaa myös riittävä jäähdytys matalilla kierrosluvuilla.

1. Etsiä riittävän tehokas tuuletin ja 3D-tulostaa sovitepala jolla sen saa karamoottorin yläosaan nykyisen akselituulettimen paikalle.
2. Johdotus niin että tuuletin käynnistyy kun kara on käynnissä, ehkä myös kierrosluvun valvonta.
3. Paremman VFD:n hankinta.

hacklabjkl-cnc-kone, 2024-11-16:
Tuuletin säätyy lämpötilan mukaan, kierrosluku nyt 2000 RPM saakka.

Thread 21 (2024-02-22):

Rakenteen jäykkyyden parantaminen

PetteriAimonen, 2024-02-22:
Tällä hetkellä jyrsimen rakenteellinen jäykkyys on eri suunnissa erilainen, ja erityisesti Y-suunnassa heikko. Alustavien mittausten perusteella ongelma on Z-akselin kelkoissa. Pidempi kelkkojen kiinnike jakaisi niihin kohdistuvan vääntömomentin paremmin.

* [ ] Jäykkyyden mittaaminen jousivaa'alla ja mittakellolla
* [ ] Uusien kelkkapidikkeiden valmistus teräslevystä
* [ ] Kelkkapidikkeiden asennus
* [ ] Jäykkyyden mittaus uudelleen

PetteriAimonen, 2024-02-27:
Samalla voisi parantaa trapetsiruuvien voitelua ja vaihtaa niihin oman servon kummallekin.

Hyvä kauppa trapetsiruuveille ja pronssimuttereille: https://www.tuli-shop.com/

PetteriAimonen, 2025-01-06:
Kelkkapidikkeiden vaihto 30 cm pitkiin tehty. Mittausten perusteella paransi ko. kohdan jäykkyyttä huomattavasti (aiemmin n. 0.05 mm heittoa 10 kg voimalla, nyt n. 0.01 mm). Kokonaisjäykkyyteen vaikutus ei ollut kovin suuri.

Closed 2025-01-06.

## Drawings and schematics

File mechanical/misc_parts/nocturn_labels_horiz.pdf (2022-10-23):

# Manual Z lift Pull belt left

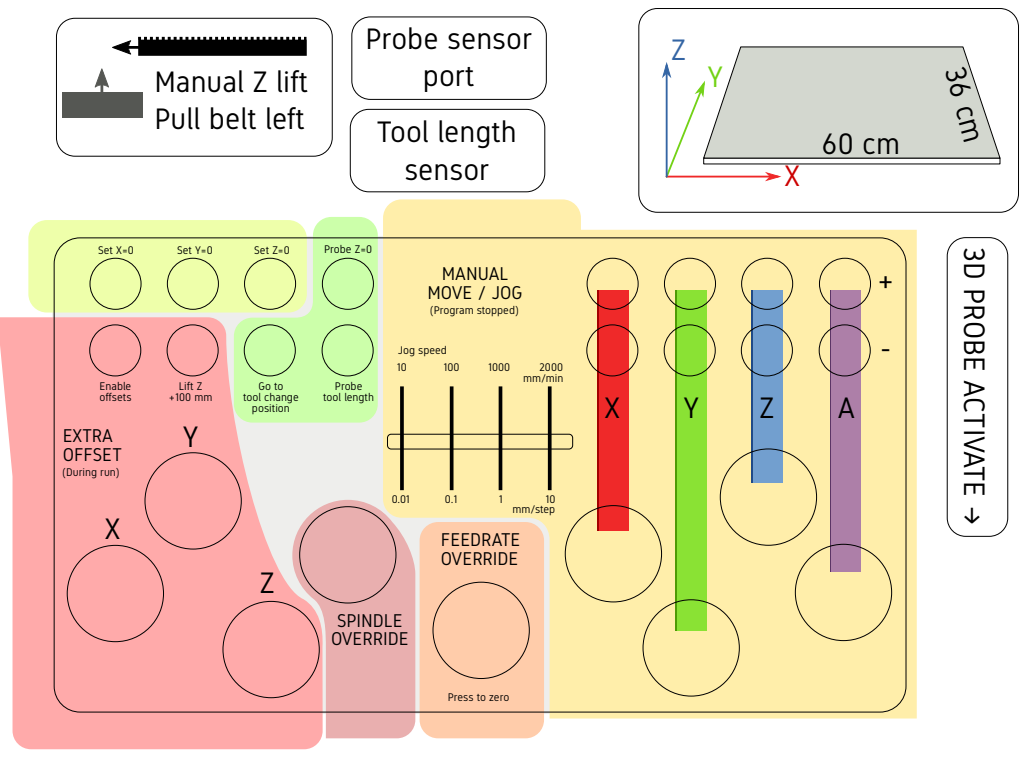
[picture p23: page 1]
mm/step; MANUAL MOVE / JOG; - mm/min; Jog speed; FEEDRATE OVERRIDE; SPINDLE OVERRIDE; EXTRA OFFSET; Enable offsets; Lift Z +100 mm; Set X=0; Set Y=0; Set Z=0; Probe Z=0; Go to tool change position; Probe tool length; (Program stopped); (During run); 3D PROBE ACTIVATE; Tool length sensor; Probe sensor; port

Press to zero

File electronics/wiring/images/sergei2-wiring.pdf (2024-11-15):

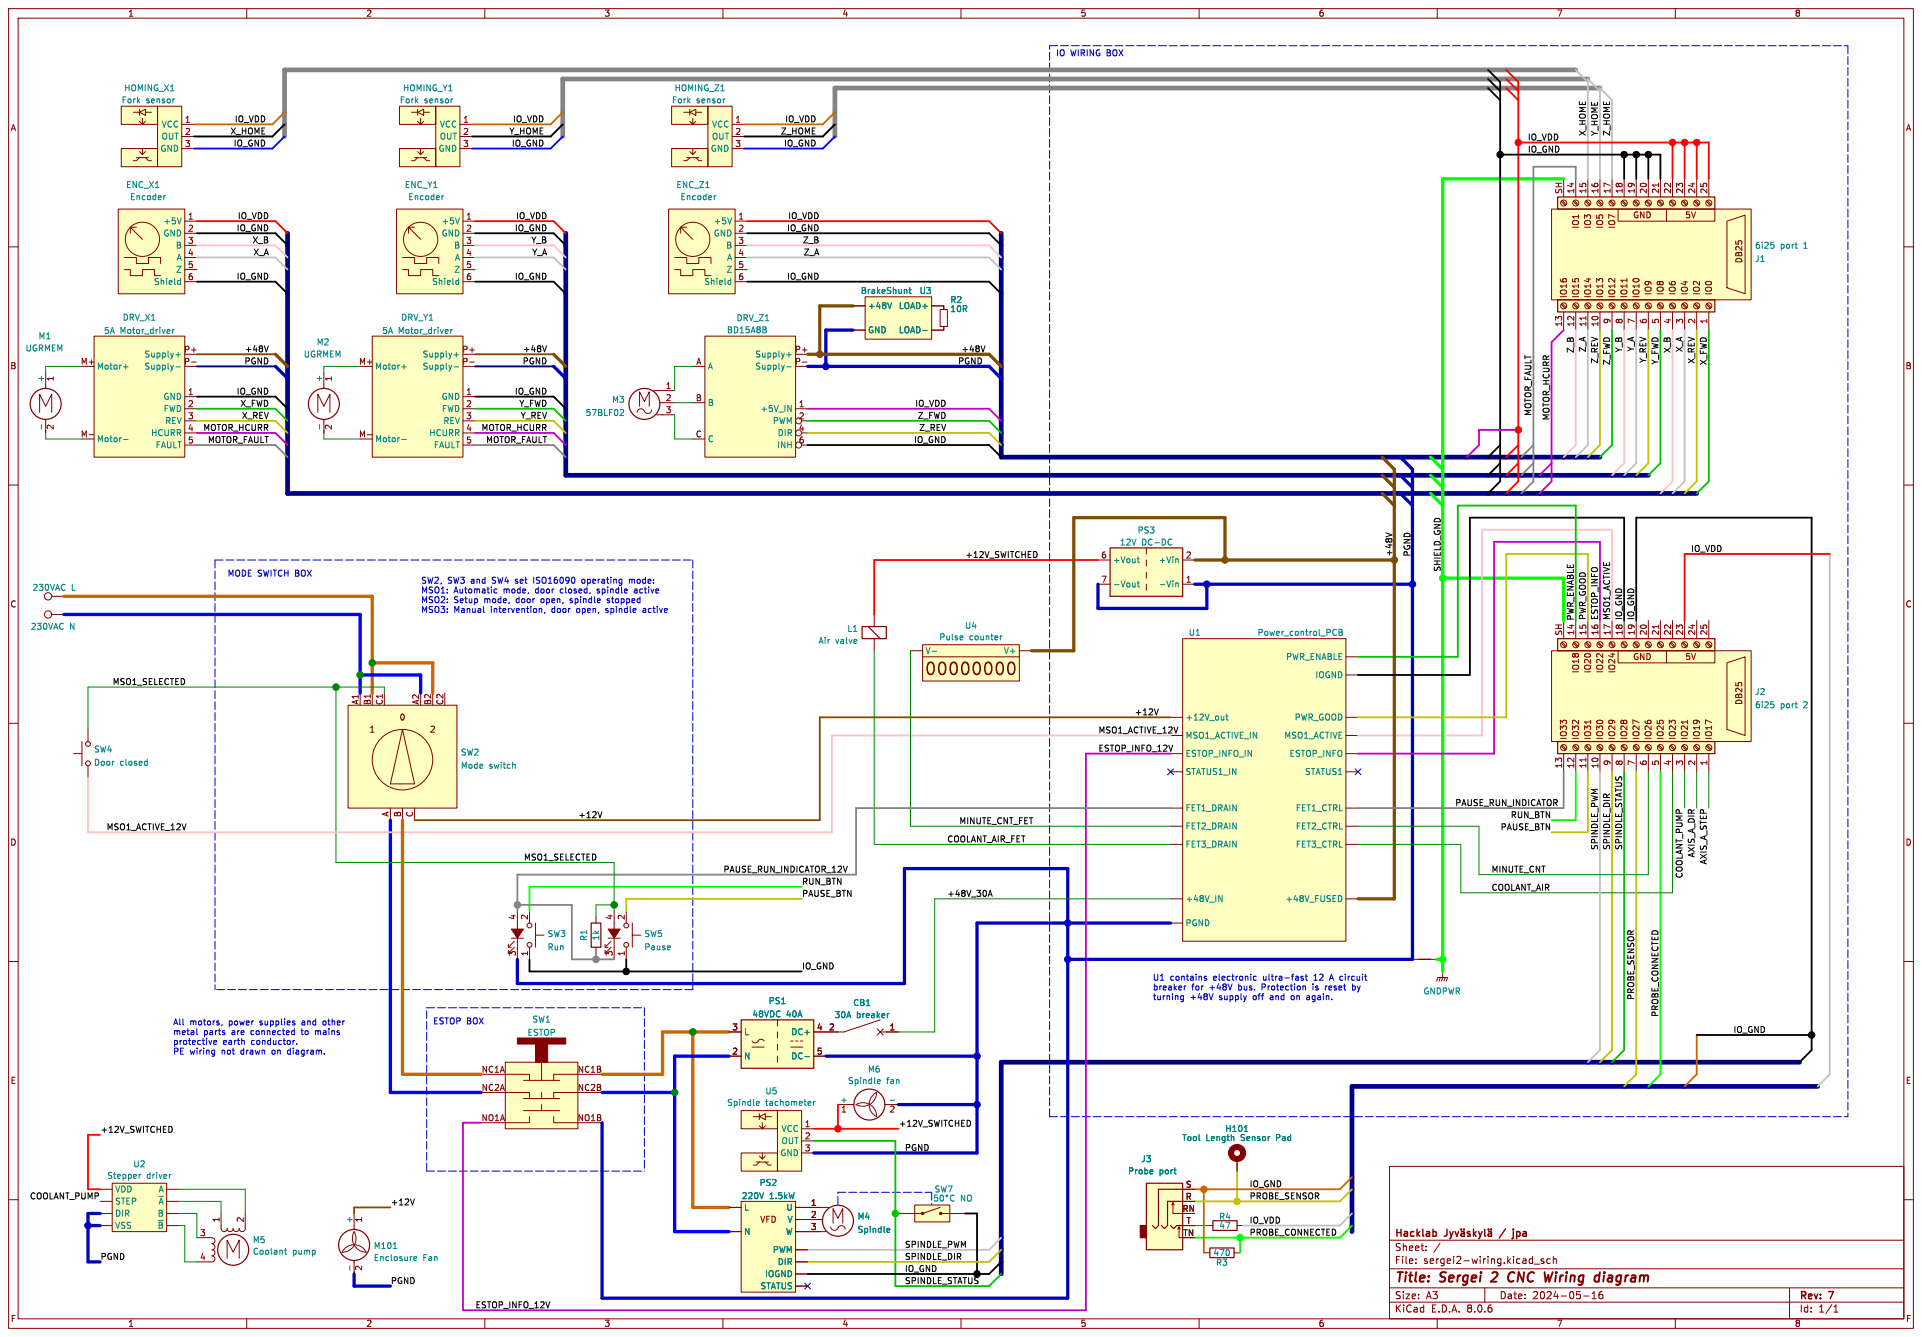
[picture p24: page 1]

OUT 2 GND 3 VCC 1 HOMING_Y1 Fork sensor +5V 1 GND 2 B

turning +48V supply off and on again.

H101 Tool Length Sensor Pad PS2

47H101 Tool Length Sensor Pad R3

Id: 1/1 Title: Sergei 2 CNC Wiring diagram

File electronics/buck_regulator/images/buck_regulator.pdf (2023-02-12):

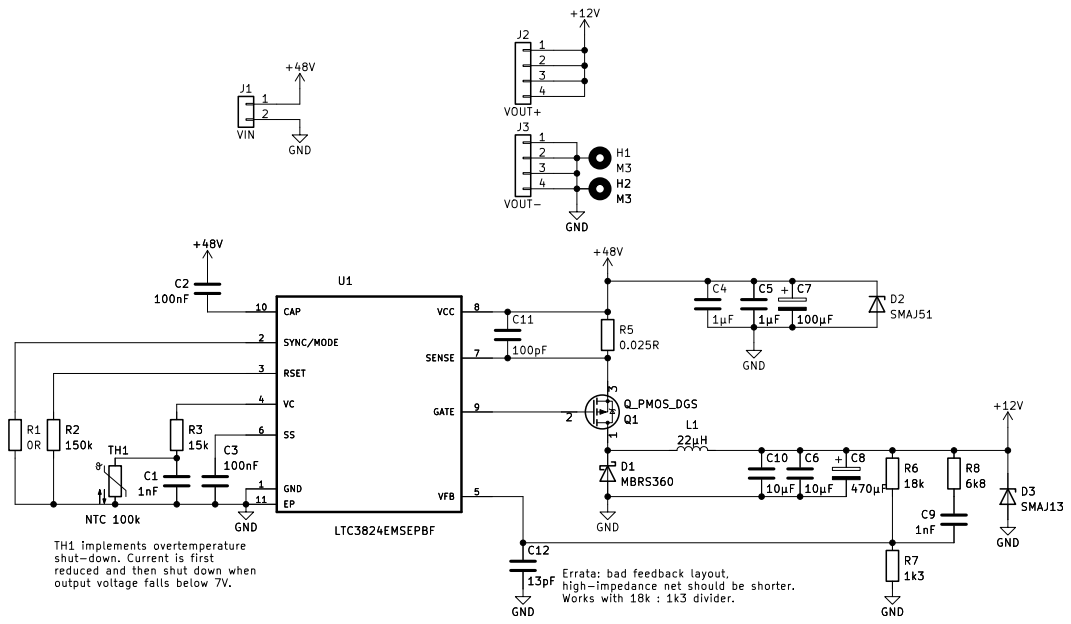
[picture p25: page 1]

high-impedance net should be shorter. Works with 18k : 1k3 divider. R2

TH1 implements overtemperature
shut-down. Current is first reduced and then shut down when

Id: 1/1 Title: 48V -> 12V buck regulator

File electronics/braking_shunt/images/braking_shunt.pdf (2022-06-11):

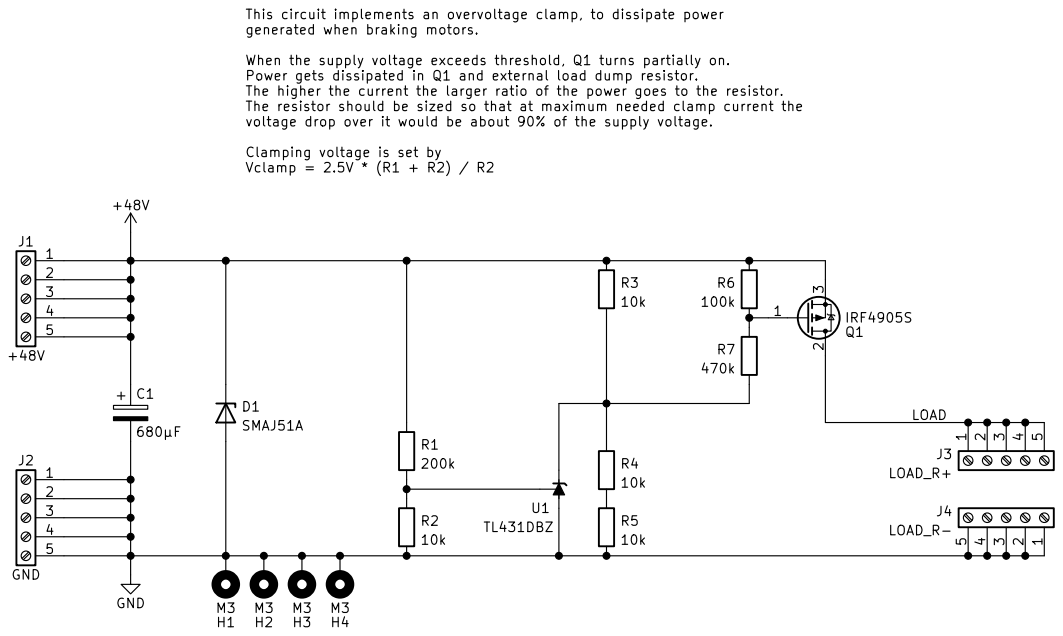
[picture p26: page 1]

This circuit implements an overvoltage clamp, to dissipate power
generated when braking motors.

When the supply voltage exceeds threshold, Q1 turns partially on.
Power gets dissipated in Q1 and external load dump resistor.
The higher the current the larger ratio of the power goes to the resistor.
The resistor should be sized so that at maximum needed clamp current the
voltage drop over it would be about 90% of the supply voltage.

Clamping voltage is set by
Vclamp = 2.5V * (R1 + R2) / R2

File: braking_shunt.kicad_sch Sheet: / Petteri Aimonen

Id: 1/1 Title: 52V / 3A overvoltage clamp

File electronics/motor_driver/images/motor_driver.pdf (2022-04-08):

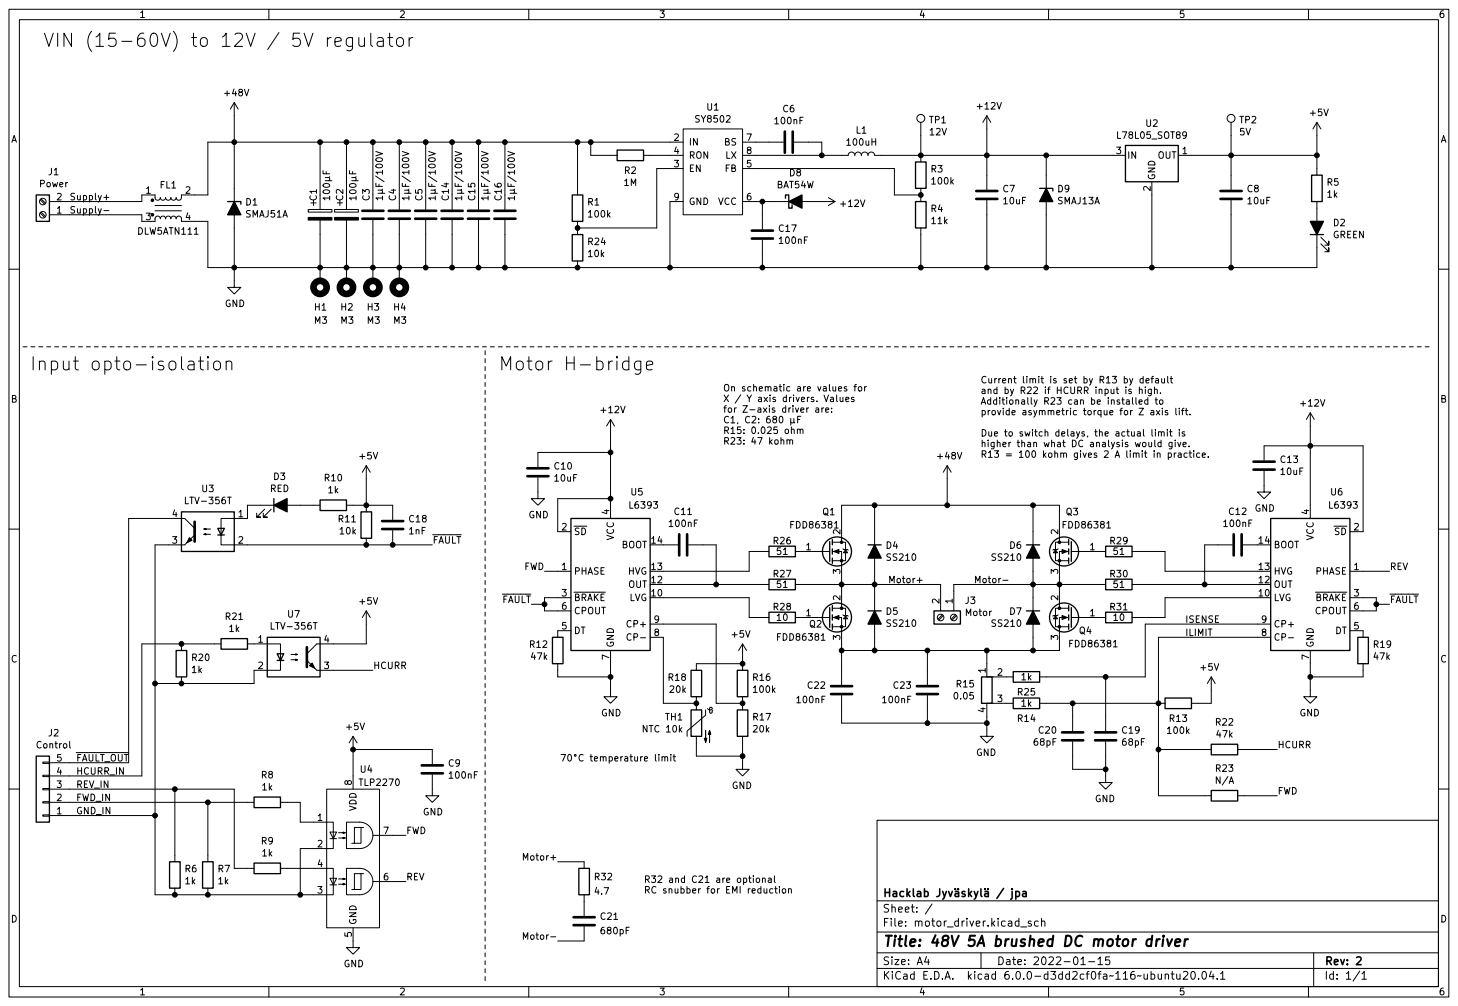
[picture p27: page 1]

VIN (15-60V) to 12V / 5V regulator
R32 and C21 are optional RC snubber for EMI reduction Motor H-bridge

R13 = 100 kohm gives 2 A limit in practice. On schematic are values for X / Y axis drivers. Values

ISENSE Current limit is set by R13 by default
and by R22 if HCURR input is high.
Additionally R23 can be installed to
provide asymmetric torque for Z axis lift.

for Z-axis driver are: þÿC1, C2: 680 µF R15: 0.025 ohm

Due to switch delays, the actual limit is
higher than what DC analysis would give.

Id: 1/1 Title: 48V 5A brushed DC motor driver

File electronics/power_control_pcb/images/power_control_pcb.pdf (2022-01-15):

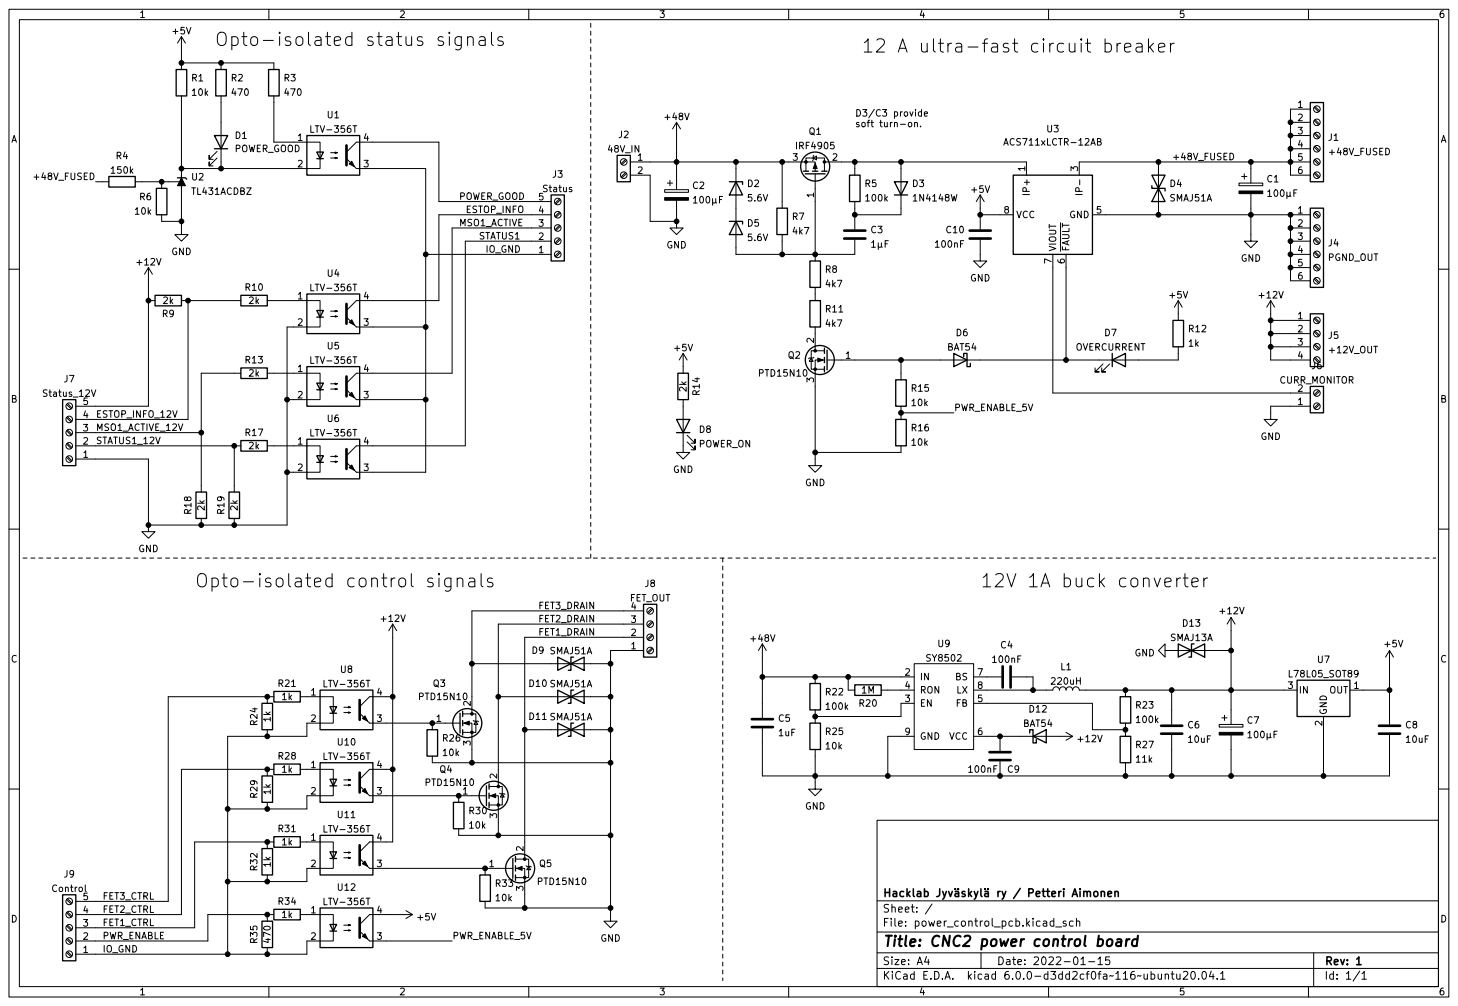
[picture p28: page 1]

soft turn-on. Opto-isolated status signals

12 A ultra-fast circuit breaker

1 IP- 3 GND 5 ~{FAULT} 6 VIOUT

Id: 1/1 Title: CNC2 power control board

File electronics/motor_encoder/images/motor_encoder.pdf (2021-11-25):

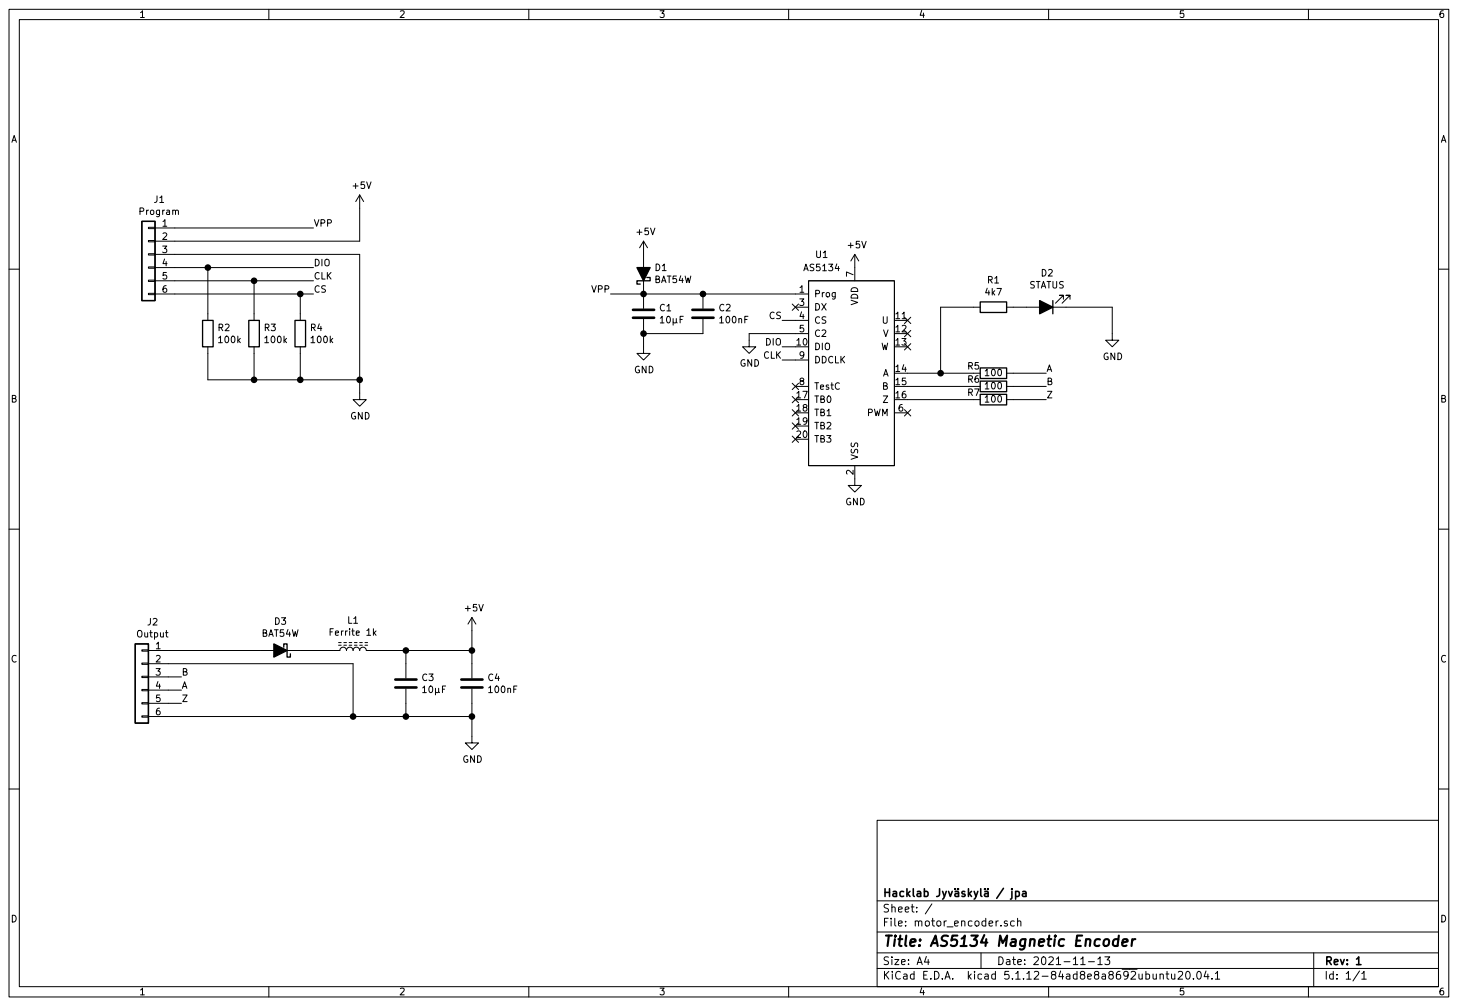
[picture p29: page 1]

2 TB3 20 DX 3 CS 4 C2 5 PWM 6 VDD

File: motor_encoder.sch Sheet: / Hacklab Jyväskylä / jpa

Id: 1/1 Title: AS5134 Magnetic Encoder

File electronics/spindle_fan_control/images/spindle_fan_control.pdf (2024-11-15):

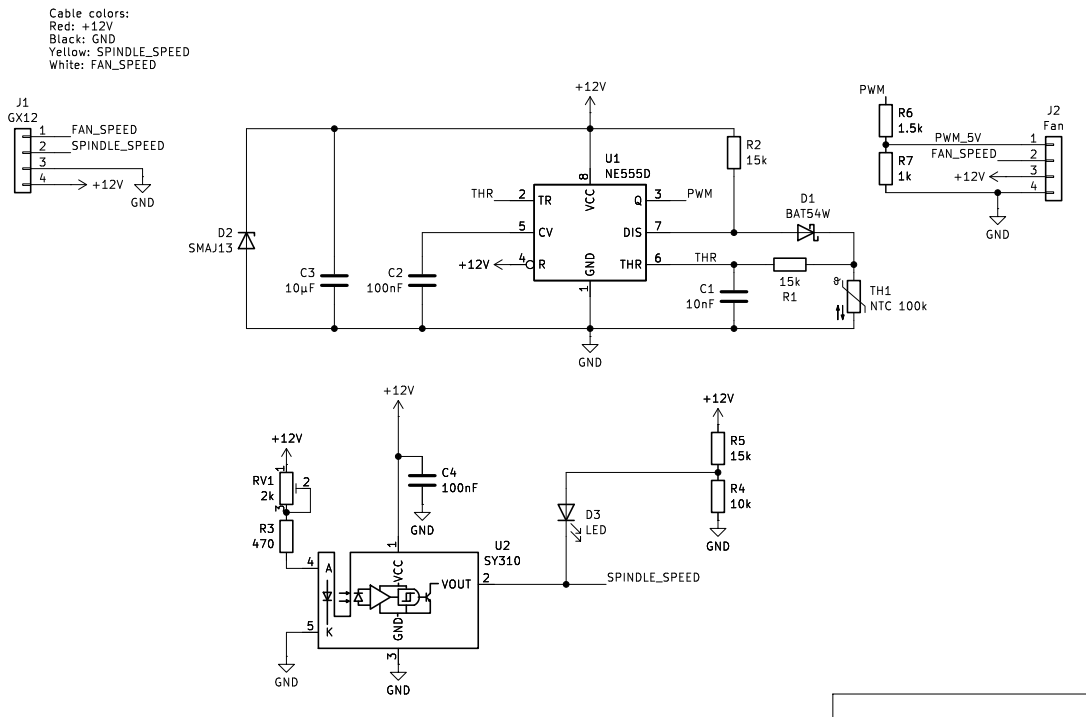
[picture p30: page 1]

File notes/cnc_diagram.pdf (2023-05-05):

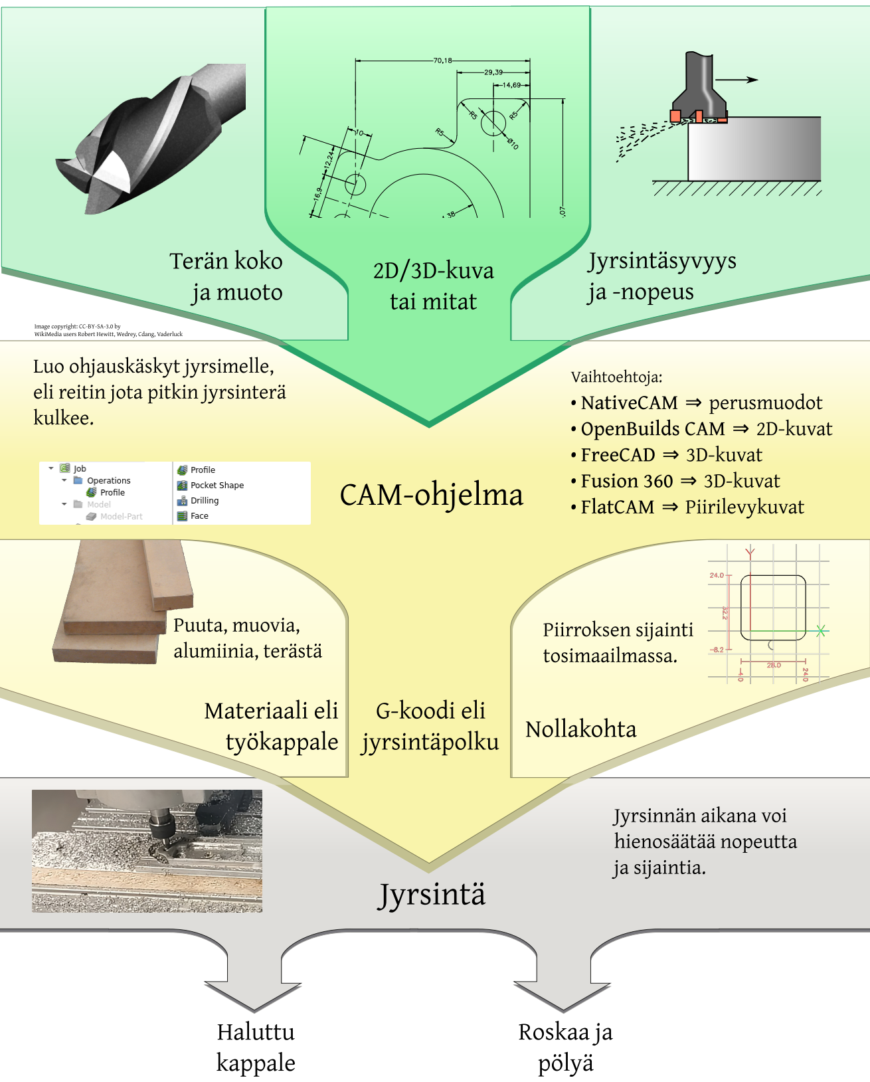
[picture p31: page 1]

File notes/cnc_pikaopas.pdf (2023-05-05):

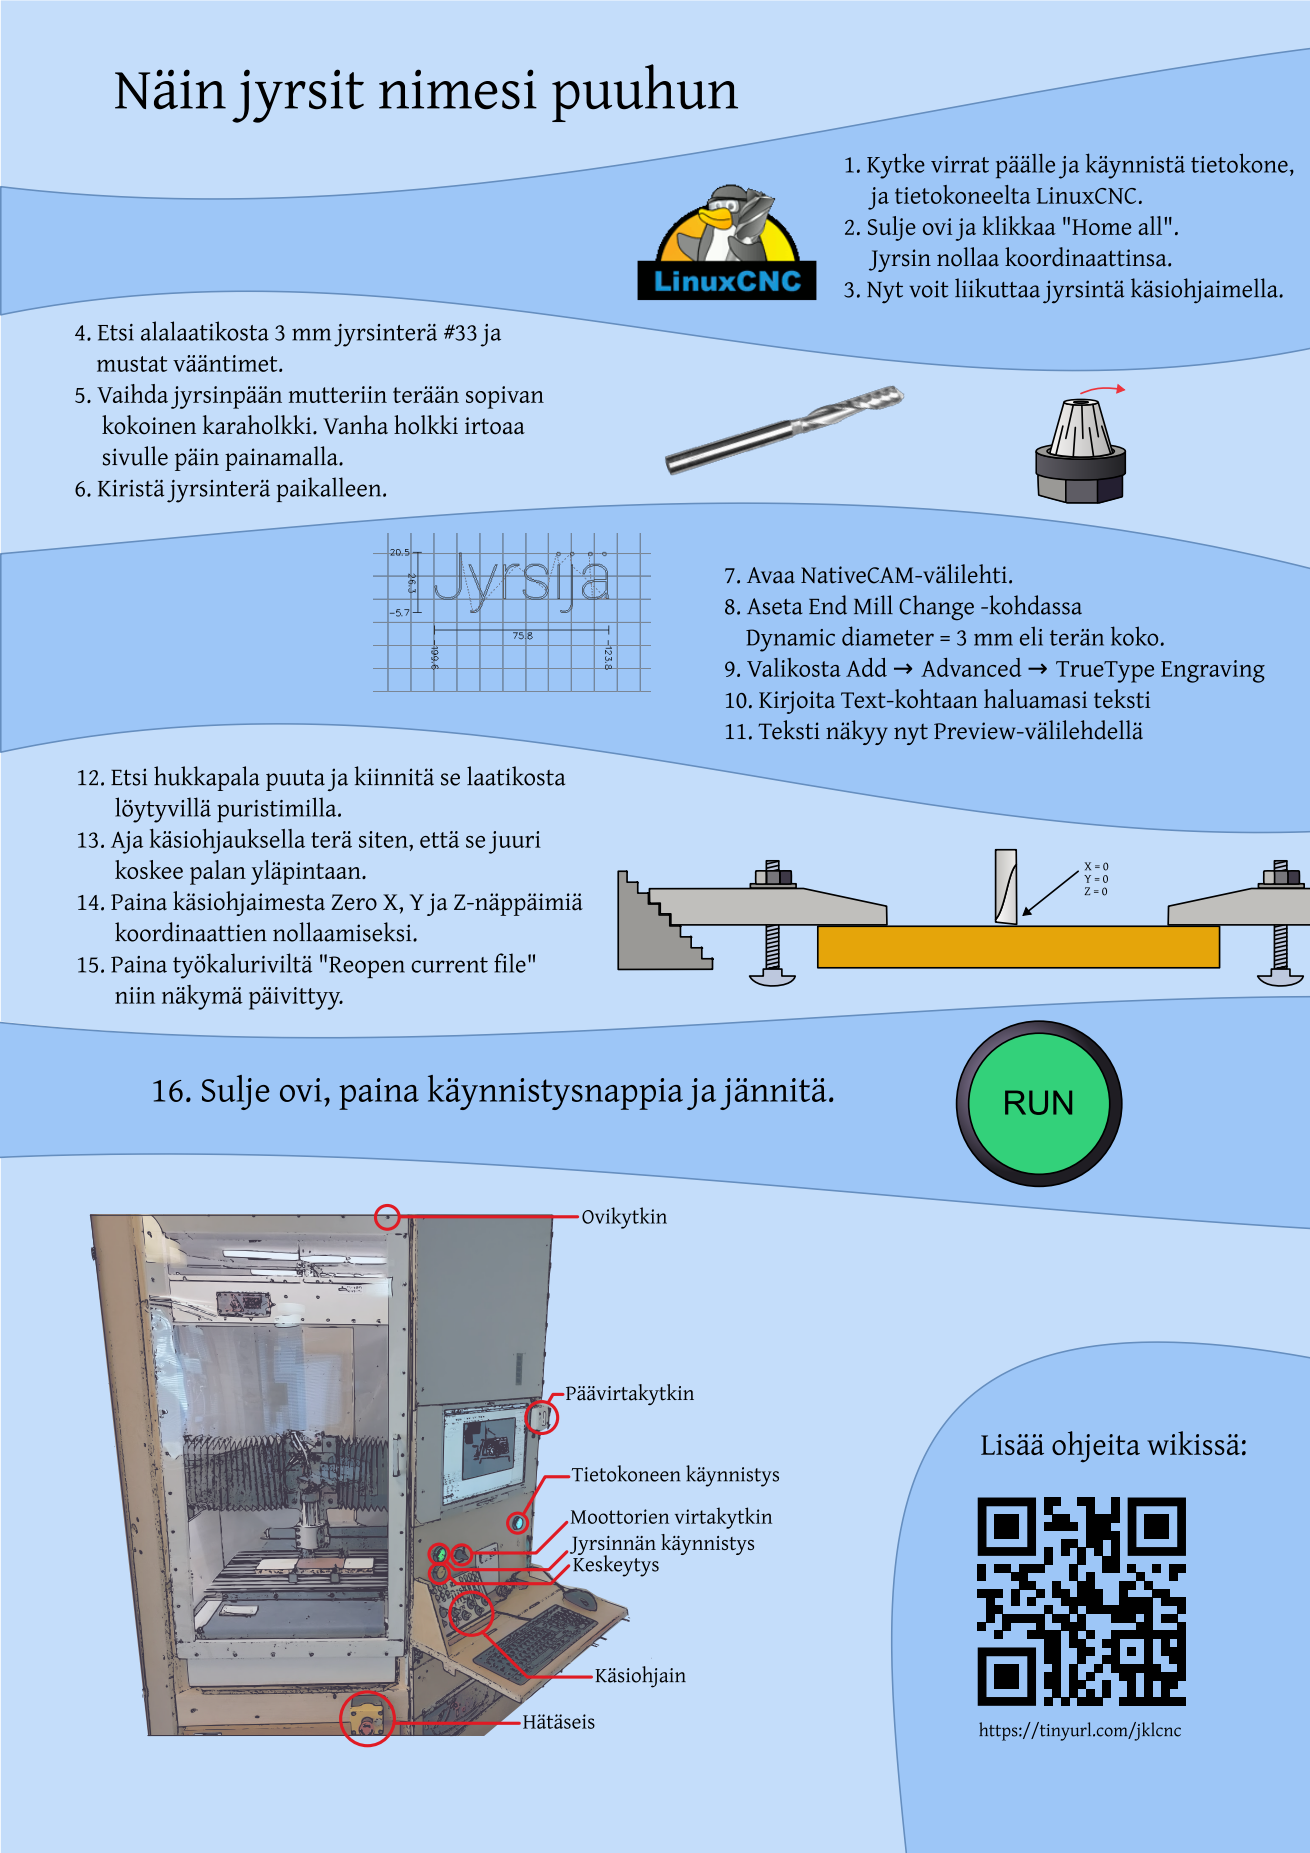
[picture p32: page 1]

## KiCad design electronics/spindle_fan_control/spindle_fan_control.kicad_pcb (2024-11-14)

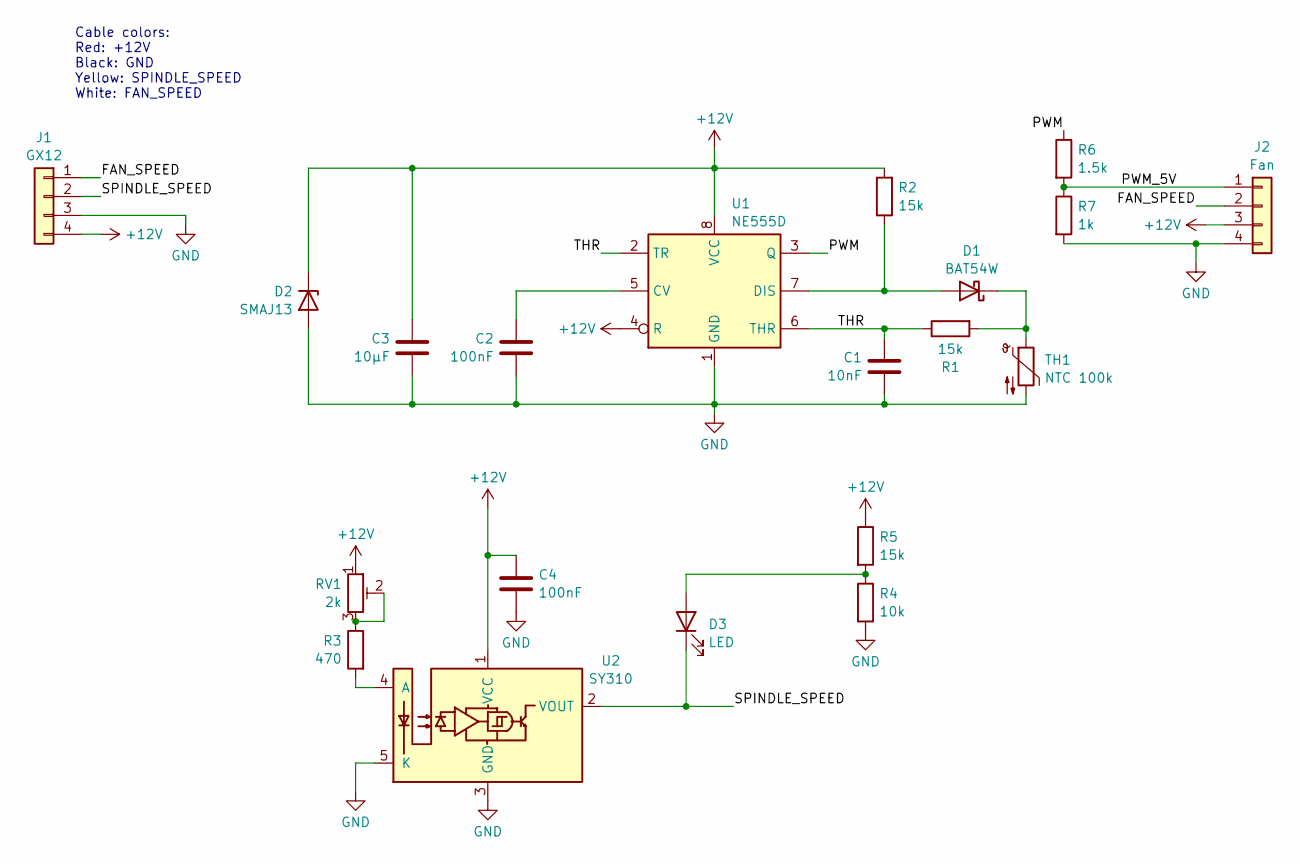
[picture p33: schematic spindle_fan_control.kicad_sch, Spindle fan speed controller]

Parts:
C1: 10nF; C_0603_1608Metric
C2, C4: 100nF; C_0603_1608Metric
C3: 10µF; C_0805_2012Metric
D1: BAT54W; D_SOD-123
D2: SMAJ13; D_SMA
D3: LED; D_0603_1608Metric
J1: GX12; PinHeader_2x02_P2.54mm_Vertical
J2: Fan; PinHeader_1x04_P2.54mm_Horizontal
R1, R2, R5: 15k; R_0603_1608Metric
R3: 470; R_0603_1608Metric
R4: 10k; R_0603_1608Metric
R6: 1.5k; R_0603_1608Metric
R7: 1k; R_0603_1608Metric
RV1: 2k; Potentiometer_Bourns_TC33X_Vertical
TH1: NTC 100k; PinHeader_1x02_P2.54mm_Vertical
U1: NE555D; SOIC-8_3.9x4.9mm_P1.27mm
U2: SY310; Kodenshi_LG206D

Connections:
+12V: C3.2, C4.2, D2.1 (K), J1.4, J2.3, R2.2, R5.1, RV1.1, U1.4 (R), U1.8 (VCC), U2.1 (VCC)
/FAN_SPEED: J1.1, J2.2
/PWM: R6.1, U1.3 (Q)
/PWM_5V: J2.1, R6.2, R7.1
/SPINDLE_SPEED: D3.1 (K), J1.2, U2.2 (VOUT)
/THR: C1.1, R1.1, U1.2 (TR), U1.6 (THR)
GND: C1.2, C2.1, C3.1, C4.1, D2.2 (A), J1.3, J2.4, R4.2, R7.2, TH1.2, U1.1 (GND), U2.3 (GND), U2.5 (K)
unnamed: D1.2 (A), R2.1, U1.7 (DIS)
unnamed: D1.1 (K), R1.2, TH1.1
unnamed: D3.2 (A), R4.1, R5.2
unnamed: R3.1, RV1.2, RV1.3
unnamed: C2.2, U1.5 (CV)
unnamed: R3.2, U2.4 (A)

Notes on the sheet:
Cable colors: Red: +12V Black: GND Yellow: SPINDLE_SPEED White: FAN_SPEED

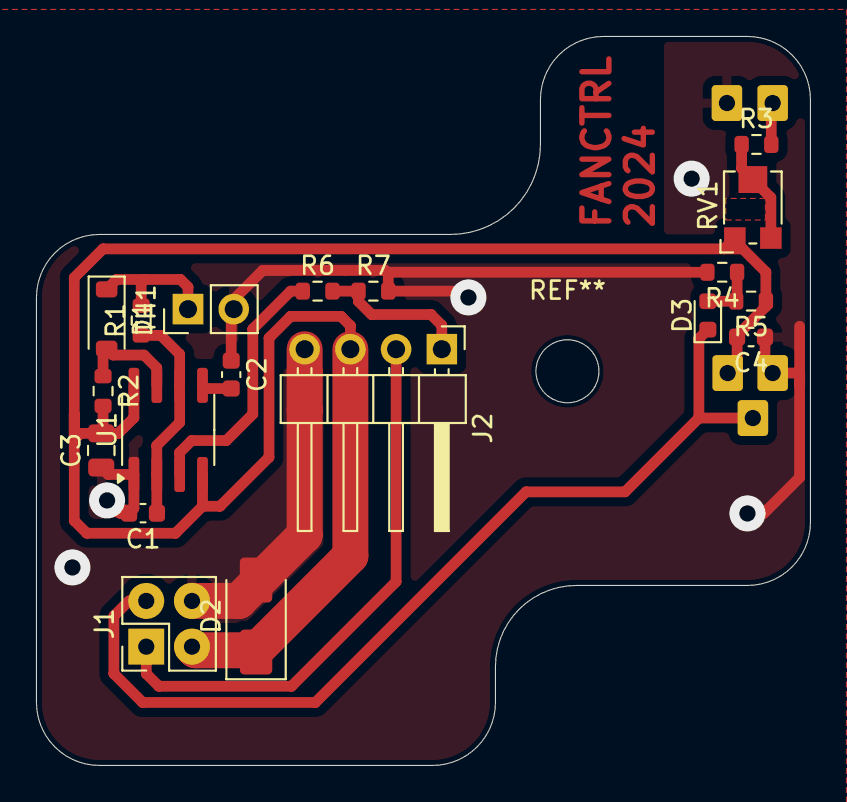
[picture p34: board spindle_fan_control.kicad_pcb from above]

Board: 2 copper layers, 43.0 x 40.5 mm, 20 parts (1 on the bottom side), 13 nets.

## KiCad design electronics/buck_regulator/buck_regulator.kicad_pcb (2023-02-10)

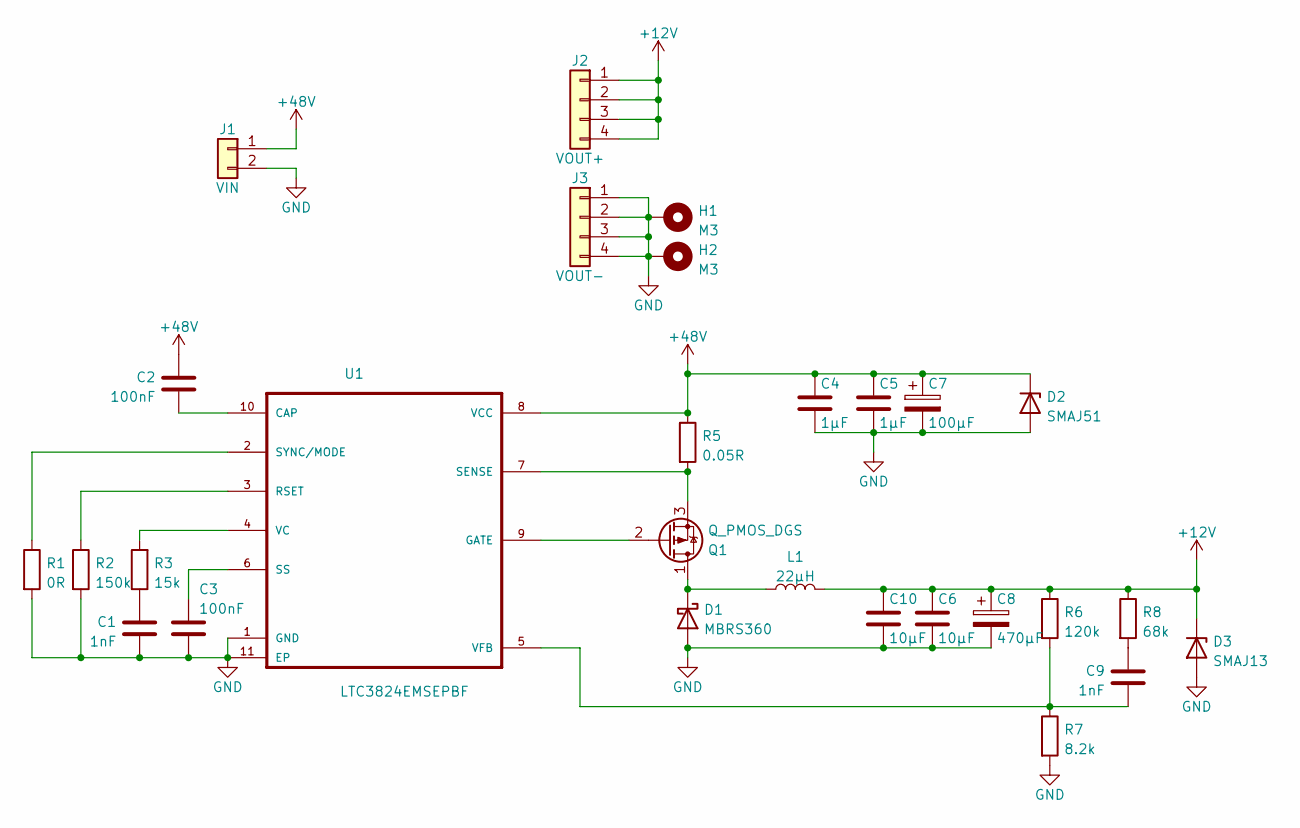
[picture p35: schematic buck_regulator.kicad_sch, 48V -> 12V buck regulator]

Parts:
C1, C9: 1nF; C_0603_1608Metric
C2, C3: 100nF; C_0603_1608Metric
C4, C5: 1µF; C_1210_3225Metric
C6, C10: 10µF; C_1206_3216Metric
C7: 100µF; CP_Radial_D10.0mm_P5.00mm
C8: 470µF; CP_Radial_D10.0mm_P5.00mm
D1: MBRS360; D_SMC
D2: SMAJ51; D_SMA
D3: SMAJ13; D_SMA
H1, H2: M3; MountingHole_3.2mm_M3_Pad
J1: VIN; TerminalBlock_Phoenix_PT-1,5-2-5.0-H_1x02_P5.00mm_Horizontal
J2: VOUT+; TerminalBlock_Phoenix_PT-1,5-4-5.0-H_1x04_P5.00mm_Horizontal
J3: VOUT-; TerminalBlock_Phoenix_PT-1,5-4-5.0-H_1x04_P5.00mm_Horizontal
L1: 22µH; L_Wuerth_HCM-1390
Q1: Q_PMOS_DGS; TSM680P06
R1: 0R; R_0603_1608Metric
R2: 150k; R_0603_1608Metric
R3: 15k; R_0603_1608Metric
R5: 0.05R; R_2512_6332Metric
R6: 120k; R_0603_1608Metric
R7: 8.2k; R_0603_1608Metric
R8: 68k; R_0603_1608Metric
U1: LTC3824EMSEPBF; MSOP-10-1EP_3x3mm_P0.5mm_EP1.68x1.88mm

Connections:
+12V: C6.1, C8.1, C10.1, D3.1 (K), J2.1, J2.2, J2.3, J2.4, L1.2, R6.1, R8.1
+48V: C2.1, C4.1, C5.1, C7.1, D2.1 (K), J1.1, R5.1, U1.8 (VCC)
GND: C1.2, C3.2, C4.2, C5.2, C6.2, C7.2, C8.2, C10.2, D1.2 (A), D2.2 (A), D3.2 (A), H1.1, H2.1, J1.2, J3.1, J3.2, J3.3, J3.4, R1.2, R2.2, R7.2, U1.1 (GND), U1.11 (EP)
unnamed: C1.1, R3.1
unnamed: C2.2, U1.10 (CAP)
unnamed: C3.1, U1.6 (SS)
unnamed: C9.1, R8.2
unnamed: C9.2, R6.2, R7.1, U1.5 (VFB)
unnamed: D1.1 (K), L1.1, Q1.1 (D)
unnamed: Q1.2 (G), U1.9 (GATE)
unnamed: Q1.3 (S), R5.2, U1.7 (SENSE)
unnamed: R1.1, U1.2 (SYNC/MODE)
unnamed: R2.1, U1.3 (RSET)
unnamed: R3.2, U1.4 (VC)

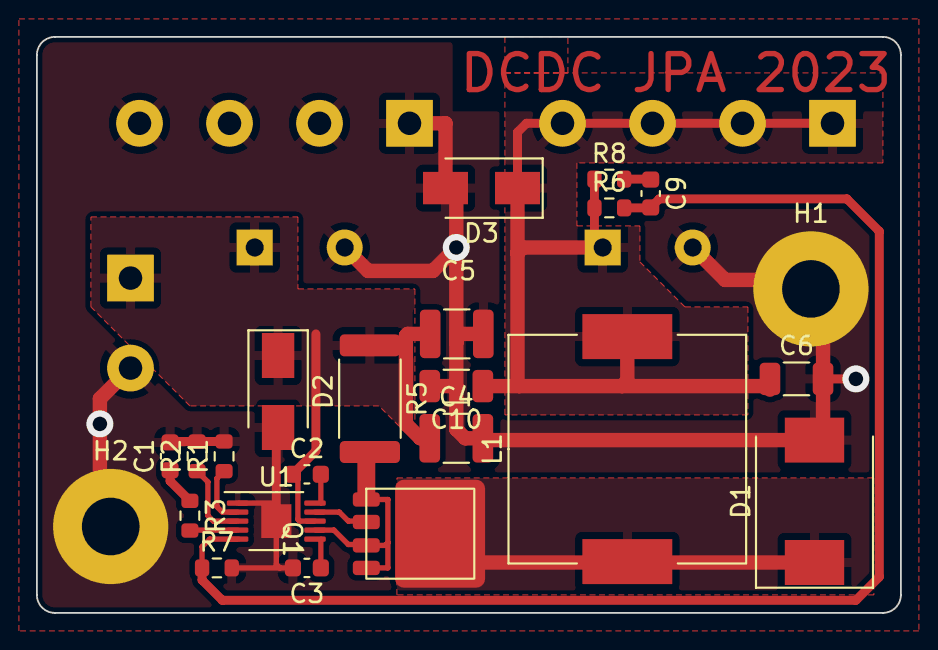
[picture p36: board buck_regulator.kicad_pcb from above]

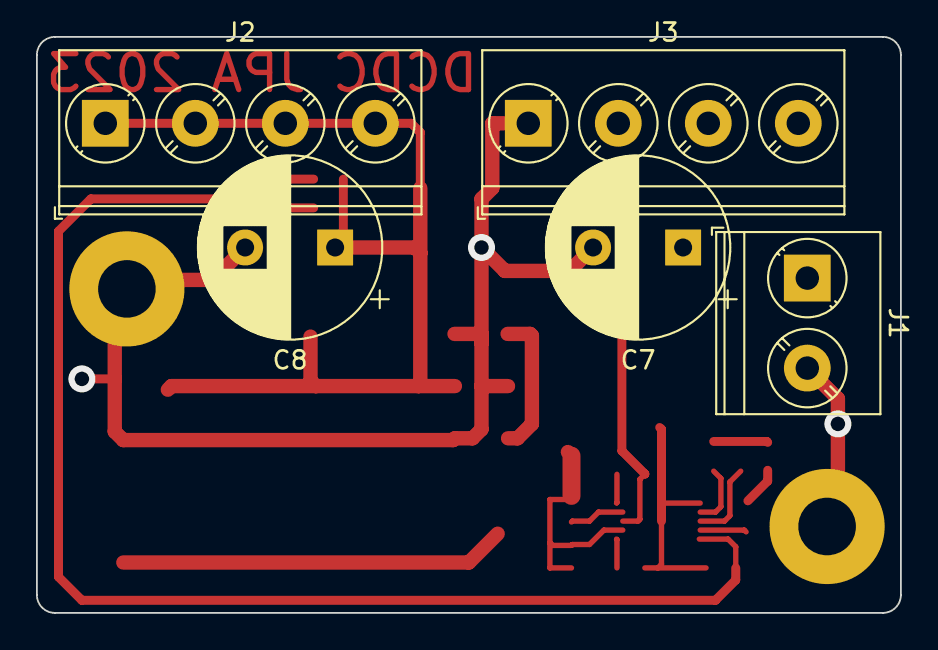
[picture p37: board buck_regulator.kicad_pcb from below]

Board: 2 copper layers, 48.0 x 32.0 mm, 28 parts (5 on the bottom side), 14 nets.

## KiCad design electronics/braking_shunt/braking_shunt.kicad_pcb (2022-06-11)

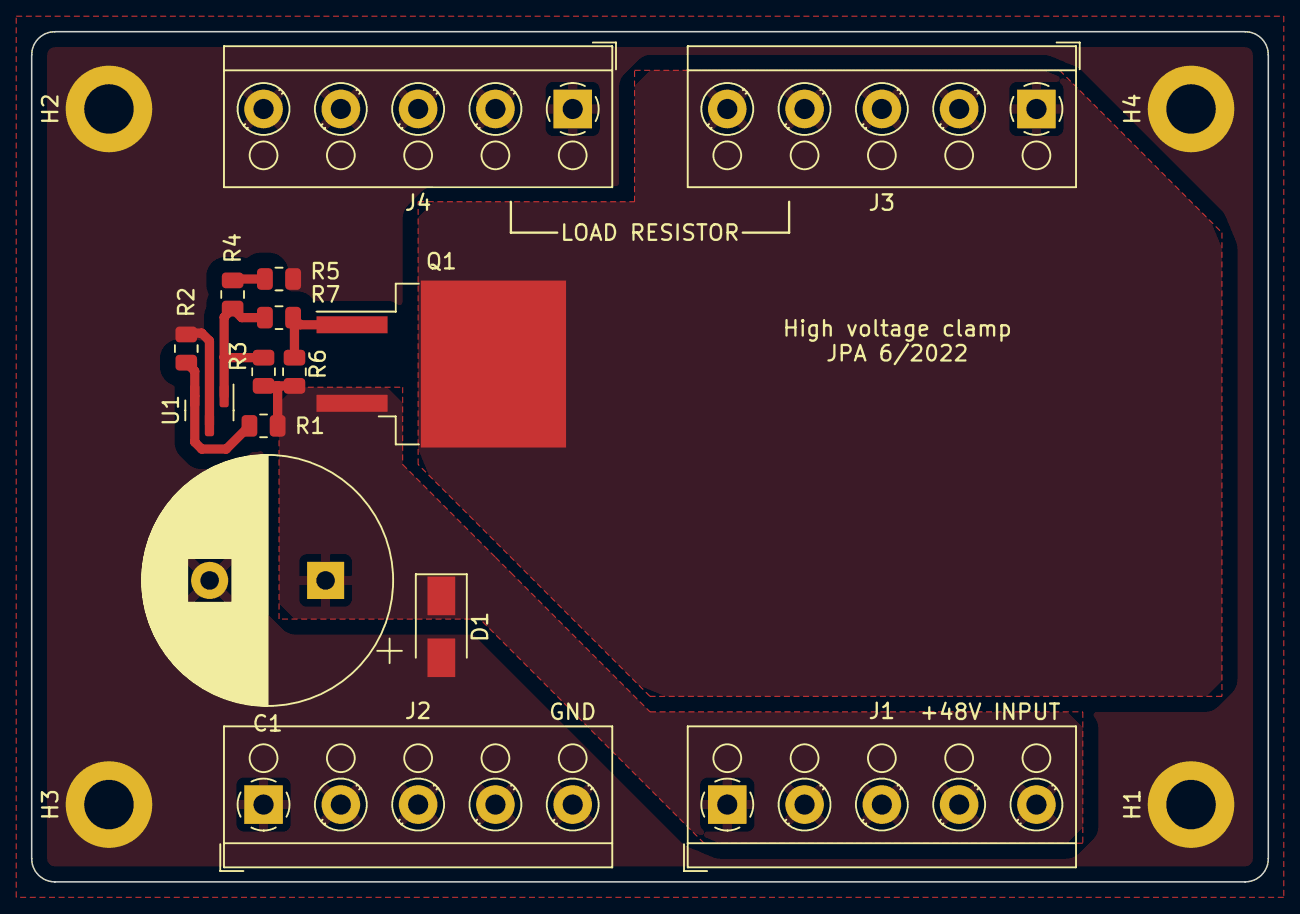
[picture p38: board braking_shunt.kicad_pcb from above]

Board: 2 copper layers, 80.0 x 55.0 mm, 19 parts (0 on the bottom side), 7 nets.

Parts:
C1: 680µF; CP_Radial_D16.0mm_P7.50mm
D1: SMAJ51A; D_SMA
H1, H2, H3, H4: M3; MountingHole_3.2mm_M3_DIN965_Pad
J1: +48V; TerminalBlock_RND_205-00004_1x05_P5.00mm_Horizontal
J2: GND; TerminalBlock_RND_205-00004_1x05_P5.00mm_Horizontal
J3: LOAD_R+; TerminalBlock_RND_205-00004_1x05_P5.00mm_Horizontal
J4: LOAD_R-; TerminalBlock_RND_205-00004_1x05_P5.00mm_Horizontal
Q1: IRF4905S; TO-263-2
R1: 200k; R_0805_2012Metric
R2, R3, R4, R5: 10k; R_0805_2012Metric
R6: 100k; R_0805_2012Metric
R7: 470k; R_0805_2012Metric
U1: TL431DBZ; SOT-23

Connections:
+48V: C1.1, D1.1 (K), J1.1, J1.2, J1.3, J1.4, J1.5, Q1.3 (S), R1.1, R3.1, R6.1
/LOAD: J3.1, J3.2, J3.3, J3.4, J3.5, Q1.2 (D)
GND: C1.2, D1.2 (A), H1.1, H2.1, H3.1, H4.1, J2.1, J2.2, J2.3, J2.4, J2.5, J4.1, J4.2, J4.3, J4.4, J4.5, R2.2, R5.2, U1.3 (A)
unnamed: Q1.1 (G), R6.2, R7.1
unnamed: R1.2, R2.1, U1.2 (REF)
unnamed: R3.2, R4.1, R7.2, U1.1 (K)
unnamed: R4.2, R5.1

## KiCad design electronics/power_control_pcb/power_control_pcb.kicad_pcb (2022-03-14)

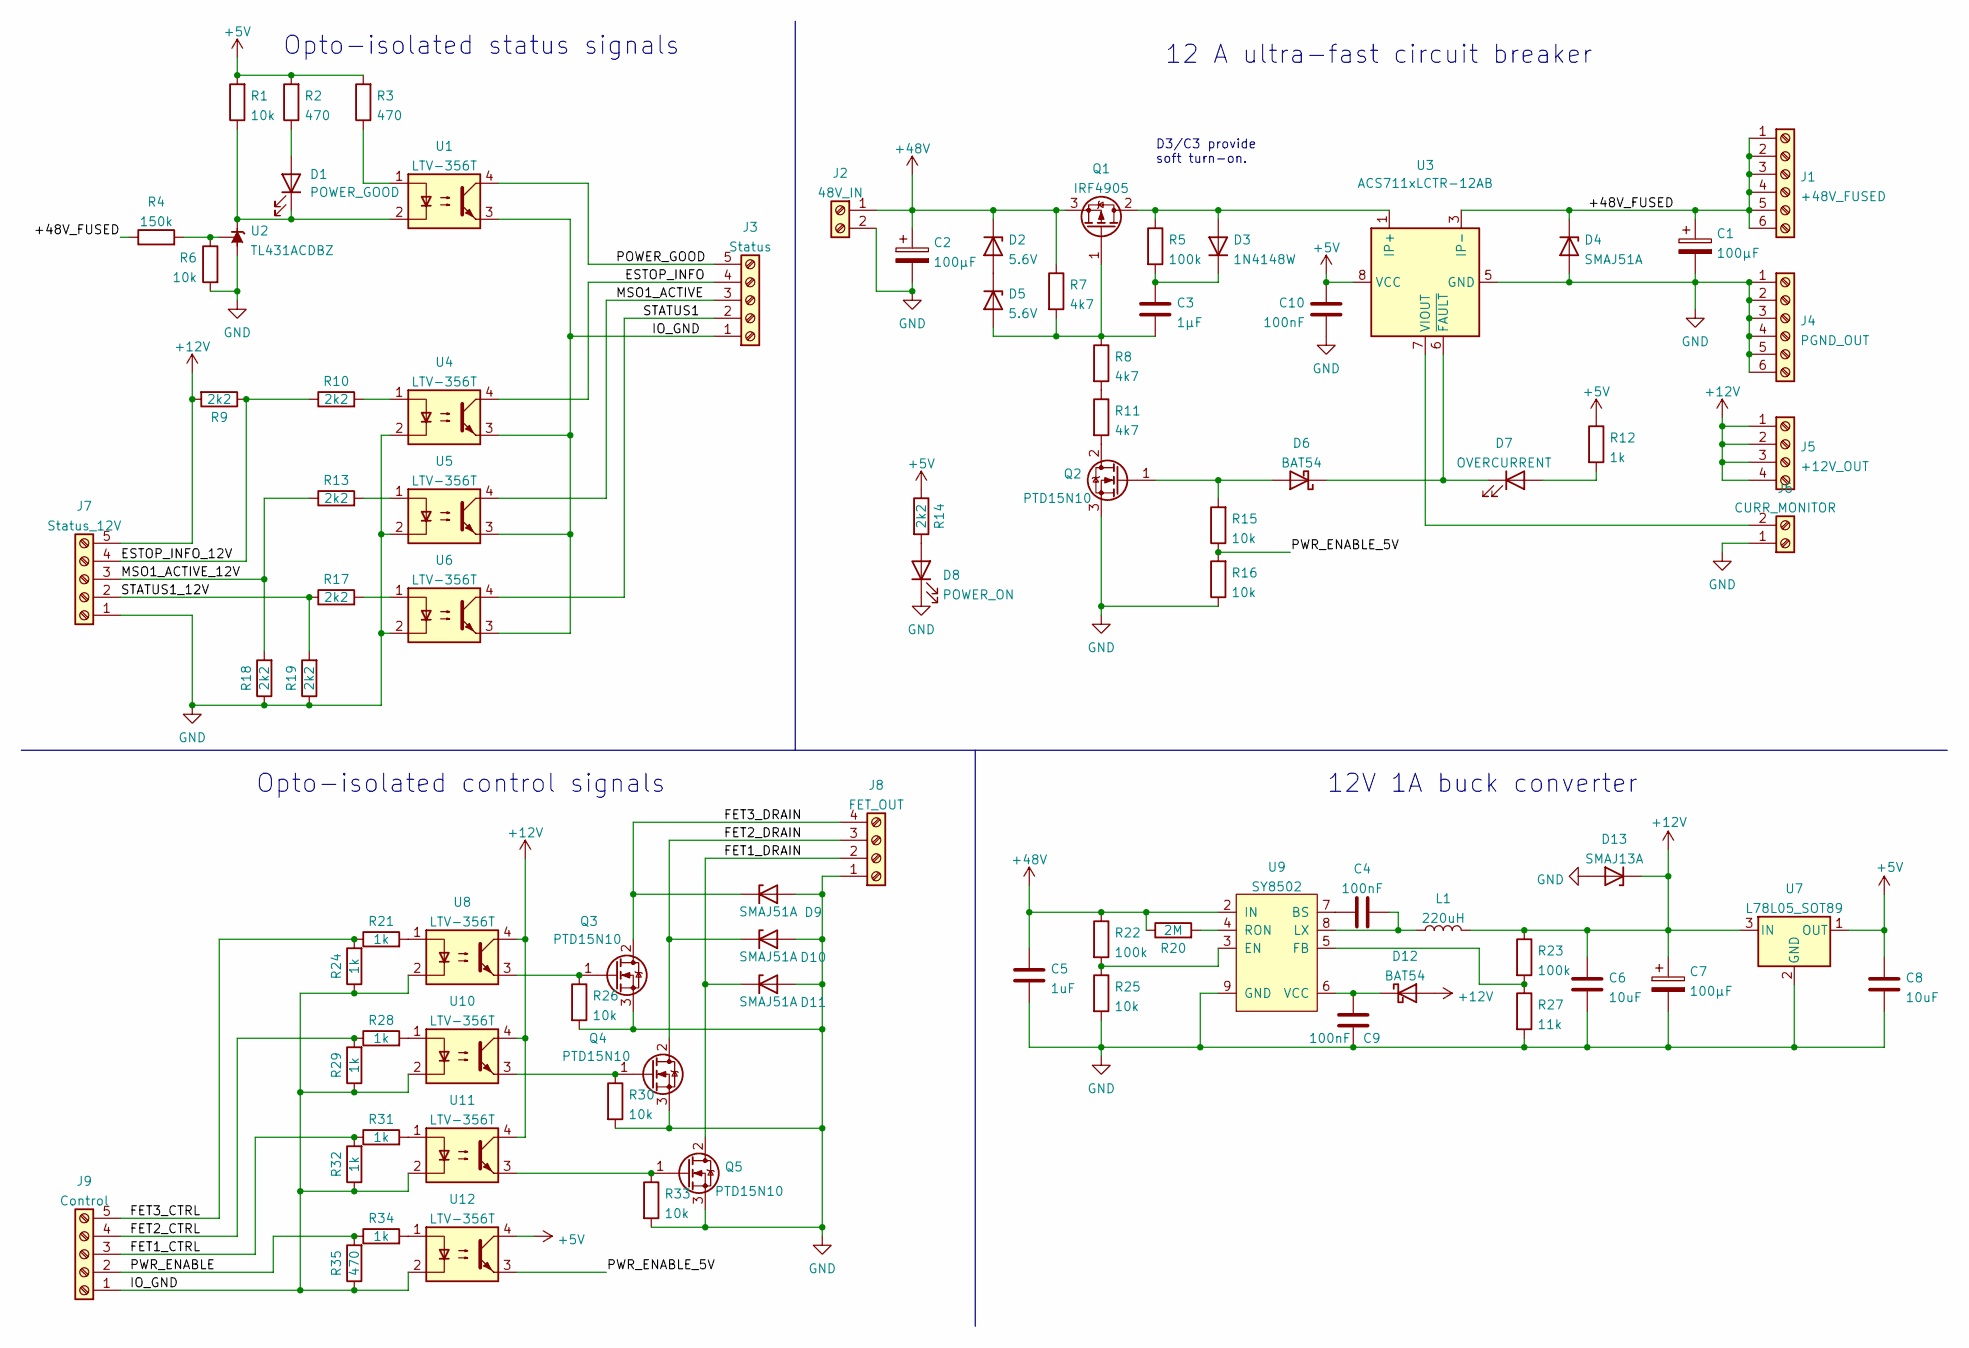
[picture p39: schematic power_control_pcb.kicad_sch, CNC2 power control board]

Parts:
C1, C2, C7: 100µF; CP_Radial_D10.0mm_P5.00mm
C3: 1µF; C_1210_3225Metric
C4, C9, C10: 100nF; C_0603_1608Metric
C5: 1uF; C_1210_3225Metric
C6, C8: 10uF; C_0805_2012Metric
D1: POWER_GOOD; LED_D3.0mm
D2, D5: 5.6V; D_SOD-123
D3: 1N4148W; D_SOD-123
D4, D9, D10, D11: SMAJ51A; D_SMA
D6, D12: BAT54; D_SOD-123
D7: OVERCURRENT; LED_D3.0mm
D8: POWER_ON; LED_D3.0mm
D13: SMAJ13A; D_SMA
J1: +48V_FUSED; TerminalBlock_Phoenix_MKDS-1,5-6_1x06_P5.00mm_Horizontal
J2: 48V_IN; TerminalBlock_Phoenix_MKDS-1,5-2_1x02_P5.00mm_Horizontal
J3: Status; TerminalBlock_TE_282834-5_1x05_P2.54mm_Horizontal
J4: PGND_OUT; TerminalBlock_Phoenix_MKDS-1,5-6_1x06_P5.00mm_Horizontal
J5: +12V_OUT; TerminalBlock_Phoenix_MKDS-1,5-4_1x04_P5.00mm_Horizontal
J6: CURR_MONITOR; TerminalBlock_Phoenix_MKDS-1,5-2_1x02_P5.00mm_Horizontal
J7: Status_12V; TerminalBlock_TE_282834-5_1x05_P2.54mm_Horizontal
J8: FET_OUT; TerminalBlock_Phoenix_MKDS-1,5-4_1x04_P5.00mm_Horizontal
J9: Control; TerminalBlock_TE_282834-5_1x05_P2.54mm_Horizontal
L1: 220uH; L_12x12mm_H6mm
Q1: IRF4905; TO-263-3_TabPin2
Q2, Q3, Q4, Q5: PTD15N10; TO-252-2
R1, R6, R15, R16, R25, R26, R30, R33: 10k; R_0603_1608Metric
R2, R3, R35: 470; R_0603_1608Metric
R4: 150k; R_0603_1608Metric
R5, R22, R23: 100k; R_0603_1608Metric
R7, R8, R11: 4k7; R_0603_1608Metric
R9, R10, R13, R14, R17, R18, R19: 2k2; R_0603_1608Metric
R12, R21, R24, R28, R29, R31, R32, R34: 1k; R_0603_1608Metric
R20: 2M; R_0603_1608Metric
R27: 11k; R_0603_1608Metric
U1, U4, U5, U6, U8, U10, U11, U12: LTV-356T; SO-4_4.4x3.6mm_P2.54mm
U2: TL431ACDBZ; SOT-23
U3: ACS711xLCTR-12AB; SOIC-8_3.9x4.9mm_P1.27mm
U7: L78L05_SOT89; SOT-89-3
U9: SY8502; SOIC-8-1EP_3.9x4.9mm_P1.27mm_EP2.29x3mm

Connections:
+5V: C8.1, C10.1, R1.2, R2.2, R3.2, R12.1, R14.1, U3.8 (VCC), U7.1 (OUT), U12.4
+12V: C6.1, C7.1, D12.2 (A), D13.1 (K), J5.1, J5.2, J5.3, J5.4, J7.5, L1.2, R9.2, R23.1, U7.3 (IN), U8.4, U10.4, U11.4
+48V: C2.1, C5.1, D2.1 (K), J2.1, Q1.3 (S), R7.1, R20.1, R22.1, U9.2 (IN)
/+48V_FUSED: C1.1, D4.1 (K), J1.1, J1.2, J1.3, J1.4, J1.5, J1.6, R4.1, U3.3 (IP-), U3.4 (IP-)
/ESTOP_INFO: J3.4, U4.4
/ESTOP_INFO_12V: J7.4, R9.1, R10.1
/FET1_CTRL: J9.3, R31.1, R32.2
/FET1_DRAIN: D11.1 (K), J8.2, Q5.2 (D)
/FET2_CTRL: J9.4, R28.1, R29.2
/FET2_DRAIN: D10.1 (K), J8.3, Q4.2 (D)
/FET3_CTRL: J9.5, R21.1, R24.2
/FET3_DRAIN: D9.1 (K), J8.4, Q3.2 (D)
/IO_GND: J3.1, J9.1, R24.1, R29.1, R32.1, R35.1, U1.3, U4.3, U5.3, U6.3, U8.2, U10.2, U11.2, U12.2
/MSO1_ACTIVE: J3.3, U5.4
/MSO1_ACTIVE_12V: J7.3, R13.1, R18.2
/POWER_GOOD: J3.5, U1.4
/PWR_ENABLE: J9.2, R34.1, R35.2
/PWR_ENABLE_5V: R15.1, R16.2, U12.3
/STATUS1: J3.2, U6.4
/STATUS1_12V: J7.2, R17.1, R19.2
GND: C1.2, C2.2, C5.2, C6.2, C7.2, C8.2, C9.2, C10.2, D4.2 (A), D8.1 (K), D9.2 (A), D10.2 (A), D11.2 (A), D13.2 (A), J2.2, J4.1, J4.2, J4.3, J4.4, J4.5, J4.6, J6.1, J7.1, J8.1, Q2.3 (S), Q3.3 (S), Q4.3 (S), Q5.3 (S), R6.2, R16.1, R18.1, R19.1, R25.2, R26.2, R27.2, R30.2, R33.2, U2.3 (A), U3.5 (GND), U4.2, U5.2, U6.2, U7.2 (GND), U9.9 (GND)
unnamed: C3.1, D3.1 (K), R5.2
unnamed: C3.2, D5.2 (A), Q1.1 (G), R7.2, R8.1
unnamed: C4.1, U9.7 (BS)
unnamed: C4.2, L1.1, U9.8 (LX)
unnamed: C9.1, D12.1 (K), U9.6 (VCC)
unnamed: D1.1 (K), R1.1, U1.2, U2.1 (K)
unnamed: D1.2 (A), R2.1
unnamed: D2.2 (A), D5.1 (K)
unnamed: D3.2 (A), Q1.2 (D), R5.1, U3.1 (IP+), U3.2 (IP+)
unnamed: D6.1 (K), D7.1 (K), U3.6 (~FAULT)
unnamed: D6.2 (A), Q2.1 (G), R15.2
unnamed: D7.2 (A), R12.2
unnamed: D8.2 (A), R14.2
unnamed: J6.2, U3.7 (VIOUT)
unnamed: Q2.2 (D), R11.2
unnamed: Q3.1 (G), R26.1, U8.3
unnamed: Q4.1 (G), R30.1, U10.3
unnamed: Q5.1 (G), R33.1, U11.3
unnamed: R3.1, U1.1
unnamed: R4.2, R6.1, U2.2 (REF)
unnamed: R10.2, U4.1
unnamed: R8.2, R11.1
unnamed: R13.2, U5.1
unnamed: R17.2, U6.1
unnamed: R20.2, U9.4 (RON)
unnamed: R21.2, U8.1
unnamed: R22.2, R25.1, U9.3 (EN)
unnamed: R23.2, R27.1, U9.5 (FB)
unnamed: R28.2, U10.1
unnamed: R31.2, U11.1
unnamed: R34.2, U12.1

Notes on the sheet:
Opto-isolated control signals
12V 1A buck converter
12 A ultra-fast circuit breaker
D3/C3 provide soft turn-on.
Opto-isolated status signals

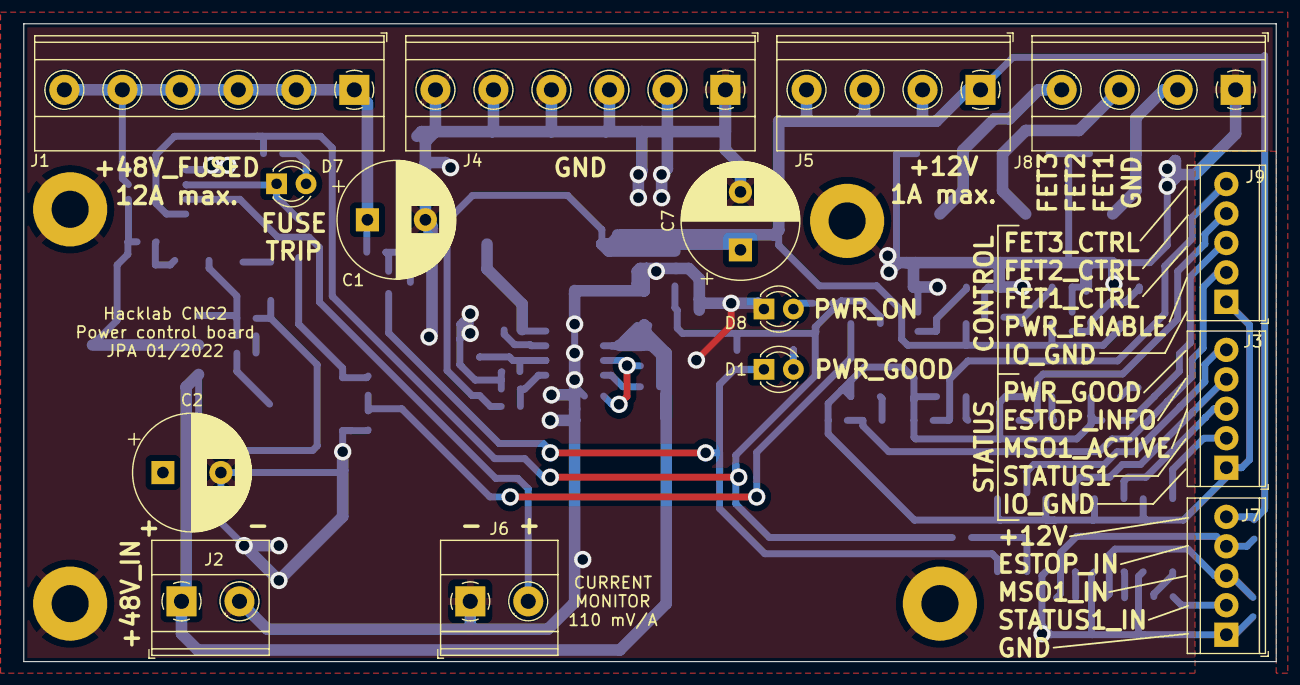
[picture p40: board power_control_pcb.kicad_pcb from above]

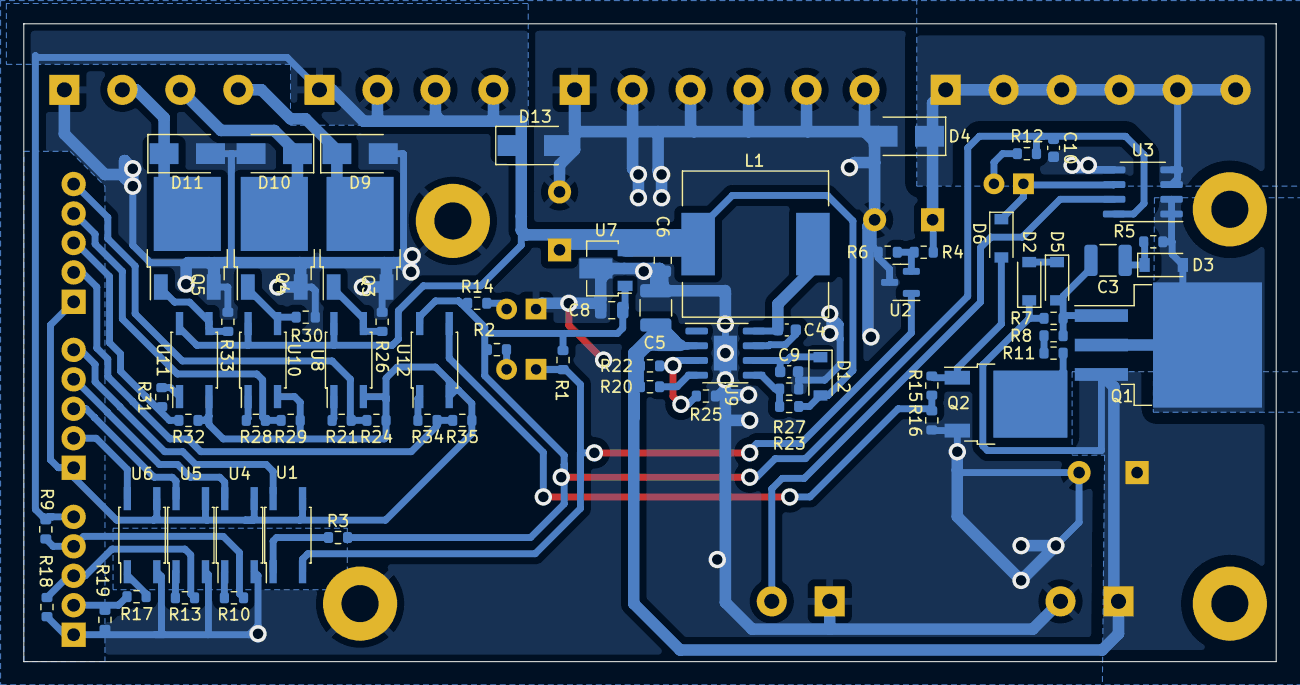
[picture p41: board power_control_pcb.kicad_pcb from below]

Board: 2 copper layers, 108.0 x 55.0 mm, 85 parts (70 on the bottom side), 52 nets.

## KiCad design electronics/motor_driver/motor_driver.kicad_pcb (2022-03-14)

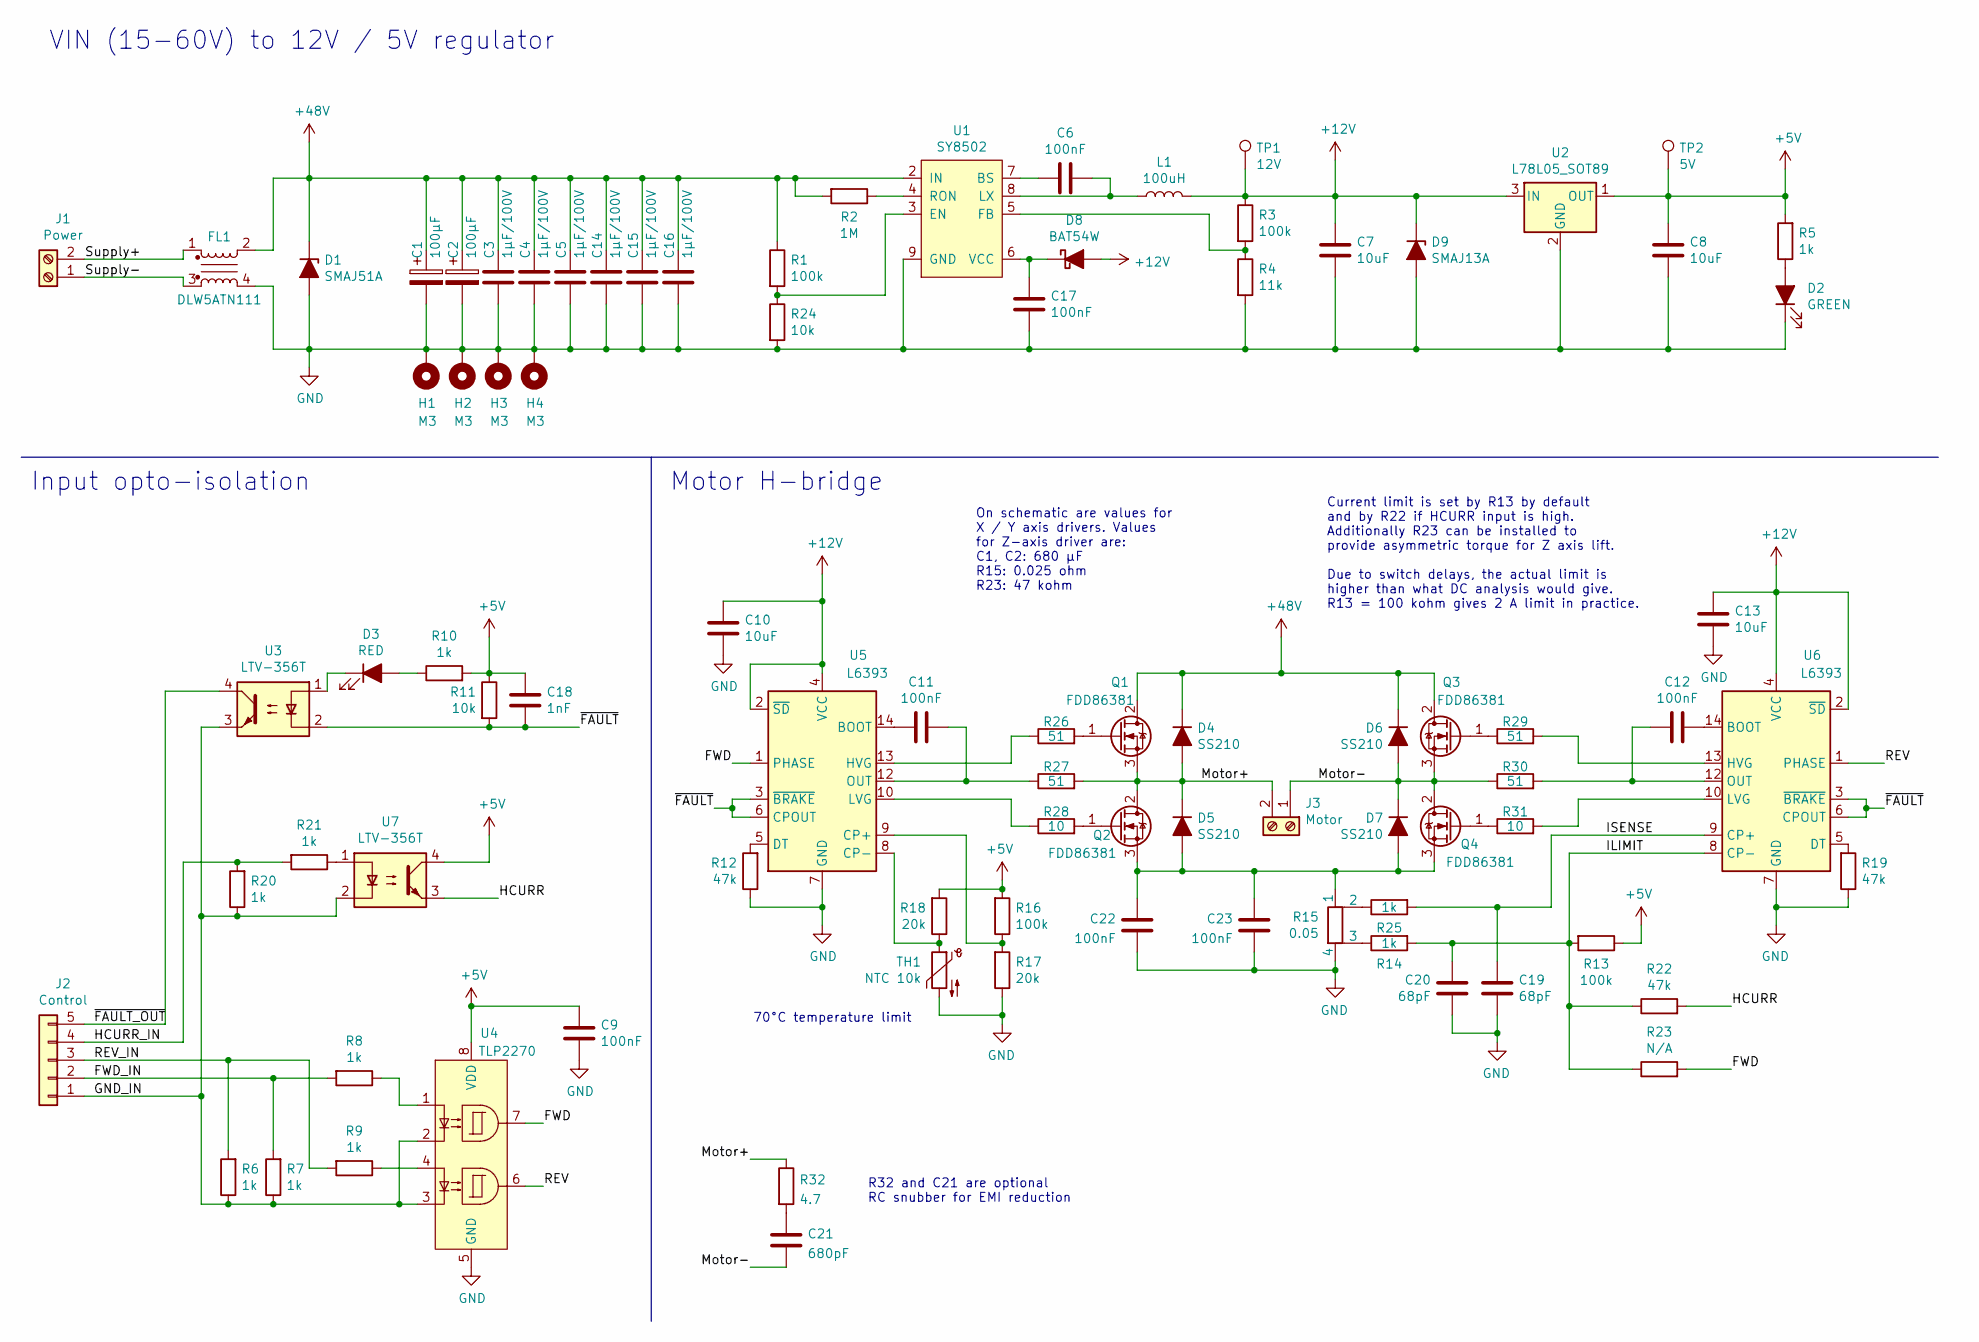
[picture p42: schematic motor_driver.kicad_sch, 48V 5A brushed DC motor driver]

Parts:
C1, C2: 100µF; CP_Radial_D10.0mm_P5.00mm_P7.50mm
C3, C4, C5, C14, C15, C16: 1µF/100V; C_1206_3216Metric
C6, C9, C11, C12, C17, C22, C23: 100nF; C_0603_1608Metric
C7, C8, C10, C13: 10uF; C_0805_2012Metric
C18: 1nF; C_0603_1608Metric
C19, C20: 68pF; C_0603_1608Metric
C21: 680pF; C_0805_2012Metric
D1: SMAJ51A; D_SMA
D2: GREEN; LED_0805_Reverse
D3: RED; LED_0805_Reverse
D4, D5, D6, D7: SS210; D_SMA
D8: BAT54W; D_SOD-123
D9: SMAJ13A; D_SMA
FL1: DLW5ATN111
H1, H2, H3, H4: M3; MountingHole_3.2mm_M3_Pad
J1: Power; TerminalBlock_bornier-2_P5.08mm
J2: Control; TerminalBlock_TE_282834-5_1x05_P2.54mm_Horizontal
J3: Motor; TerminalBlock_bornier-2_P5.08mm
L1: 100uH; L_Bourns-SRN4018
Q1, Q2, Q3, Q4: FDD86381; TO-252-2
R1, R3, R13, R16: 100k; R_0603_1608Metric
R2: 1M; R_0603_1608Metric
R4: 11k; R_0603_1608Metric
R5, R6, R7, R8, R9, R10, R14, R20, R21, R25: 1k; R_0603_1608Metric
R11, R24: 10k; R_0603_1608Metric
R12, R19, R22: 47k; R_0603_1608Metric
R15: 0.05; Shunt_2512
R17, R18: 20k; R_0603_1608Metric
R23: N/A; R_0603_1608Metric
R26, R27, R29, R30: 51; R_0603_1608Metric
R28, R31: 10; R_0603_1608Metric
R32: 4.7; R_0805_2012Metric
TH1: NTC 10k; R_0603_1608Metric
TP1: 12V; TestPoint_Pad_D2.0mm
TP2: 5V; TestPoint_Pad_D2.0mm
U1: SY8502; SOIC-8-1EP_3.9x4.9mm_P1.27mm_EP2.514x3.2mm
U2: L78L05_SOT89; SOT-89-3
U3, U7: LTV-356T; SO-4_4.4x3.6mm_P2.54mm
U4: TLP2270; SOIC-8_7.5x5.85mm_P1.27mm
U5, U6: L6393; SO-14_3.9x8.65mm_P1.27mm

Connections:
+5V: C8.1, C9.1, C18.1, R5.2, R10.2, R11.1, R13.1, R16.2, R18.2, TP2.1, U2.1 (OUT), U4.8 (VDD), U7.4
+12V: C7.1, C10.1, C13.1, D8.2 (A), D9.1 (K), L1.1, R3.1, TP1.1, U2.3 (IN), U5.2 (~SD), U5.4 (VCC), U6.2 (~SD), U6.4 (VCC)
+48V: C1.1, C2.1, C3.1, C4.1, C5.1, C14.1, C15.1, C16.1, D1.1 (K), D4.1 (K), D6.1 (K), FL1.2, Q1.2 (D), Q3.2 (D), R1.1, R2.2, U1.2 (IN)
/FWD: R23.2, U4.7, U5.1 (PHASE)
/FWD_IN: J2.2, R7.2, R8.2
/GND_IN: J2.1, R6.1, R7.1, R20.1, U3.3, U4.2, U4.3, U7.2
/HCURR: R22.2, U7.3
/HCURR_IN: J2.4, R20.2, R21.2
/ILIMIT: C20.1, R13.2, R14.2, R22.1, R23.1, U6.8 (CP-)
/ISENSE: C19.1, R25.2, U6.9 (CP+)
/Motor+: D4.2 (A), D5.1 (K), J3.2, Q1.3 (S), Q2.2 (D), R27.2, R32.1
/Motor-: C21.2, D6.2 (A), D7.1 (K), J3.1, Q3.3 (S), Q4.2 (D), R30.1
/REV: U4.6, U6.1 (PHASE)
/REV_IN: J2.3, R6.2, R9.2
/Supply+: FL1.1, J1.2
/Supply-: FL1.3, J1.1
/~FAULT_OUT: J2.5, U3.4
/~FAULT: C18.2, R11.2, U3.2, U5.3 (~BRAKE), U5.6 (CPOUT), U6.3 (~BRAKE), U6.6 (CPOUT)
GND: C1.2, C2.2, C3.2, C4.2, C5.2, C7.2, C8.2, C9.2, C10.2, C13.2, C14.2, C15.2, C16.2, C17.1, C19.2, C20.2, C22.2, C23.2, D1.2 (A), D2.1 (K), D9.2 (A), FL1.4, H1.1, H2.1, H3.1, H4.1, R4.2, R12.1, R15.4, R17.1, R19.1, R24.2, TH1.2, U1.9 (GND), U2.2 (GND), U4.5 (GND), U5.7 (GND), U6.7 (GND)
unnamed: C6.1, L1.2, U1.8 (LX)
unnamed: C6.2, U1.7 (BS)
unnamed: C11.1, R27.1, U5.12 (OUT)
unnamed: C11.2, U5.14 (BOOT)
unnamed: C12.1, R30.2, U6.12 (OUT)
unnamed: C12.2, U6.14 (BOOT)
unnamed: C17.2, D8.1 (K), U1.6 (VCC)
unnamed: C21.1, R32.2
unnamed: D2.2 (A), R5.1
unnamed: D3.1 (K), U3.1
unnamed: D3.2 (A), R10.1
unnamed: C22.1, C23.1, D5.2 (A), D7.2 (A), Q2.3 (S), Q4.3 (S), R15.1
unnamed: Q1.1 (G), R26.2
unnamed: Q2.1 (G), R28.2
unnamed: Q3.1 (G), R29.1
unnamed: Q4.1 (G), R31.1
unnamed: R1.2, R24.1, U1.3 (EN)
unnamed: R2.1, U1.4 (RON)
unnamed: R3.2, R4.1, U1.5 (FB)
unnamed: R8.1, U4.1
unnamed: R9.1, U4.4
unnamed: R12.2, U5.5 (DT)
unnamed: R14.1, R15.3
unnamed: R15.2, R25.1
unnamed: R16.1, R17.2, U5.9 (CP+)
unnamed: R18.1, TH1.1, U5.8 (CP-)
unnamed: R19.2, U6.5 (DT)
unnamed: R21.1, U7.1
unnamed: R26.1, U5.13 (HVG)
unnamed: R28.1, U5.10 (LVG)
unnamed: R29.2, U6.13 (HVG)
unnamed: R31.2, U6.10 (LVG)

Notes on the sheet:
Input opto-isolation
VIN (15-60V) to 12V / 5V regulator
Current limit is set by R13 by default and by R22 if HCURR input is high. Additionally R23 can be installed to provide asymmetric torque for Z axis lift. Due to switch delays, the actual limit is higher than what DC analysis would give. R13 = 100 kohm gives 2 A limit in practice.
70°C temperature limit
Motor H-bridge
R32 and C21 are optional RC snubber for EMI reduction
On schematic are values for X / Y axis drivers. Values for Z-axis driver are: C1, C2: 680 µF R15: 0.025 ohm R23: 47 kohm

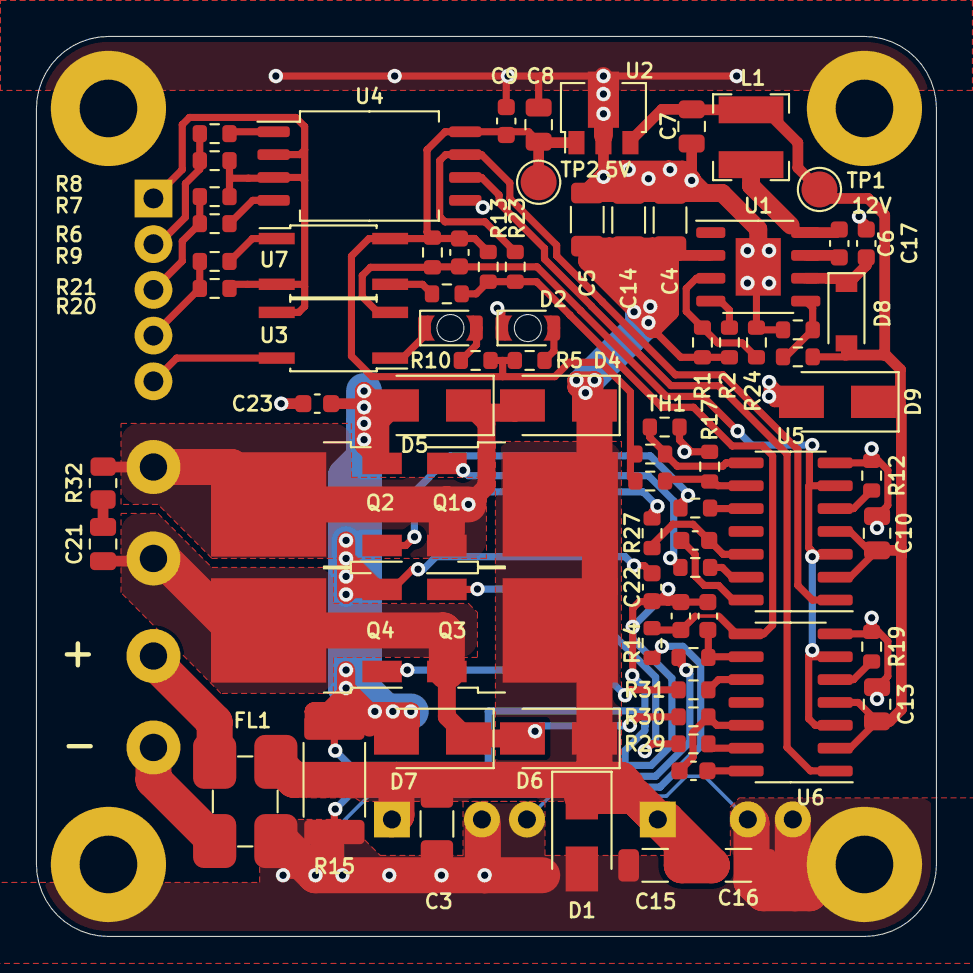
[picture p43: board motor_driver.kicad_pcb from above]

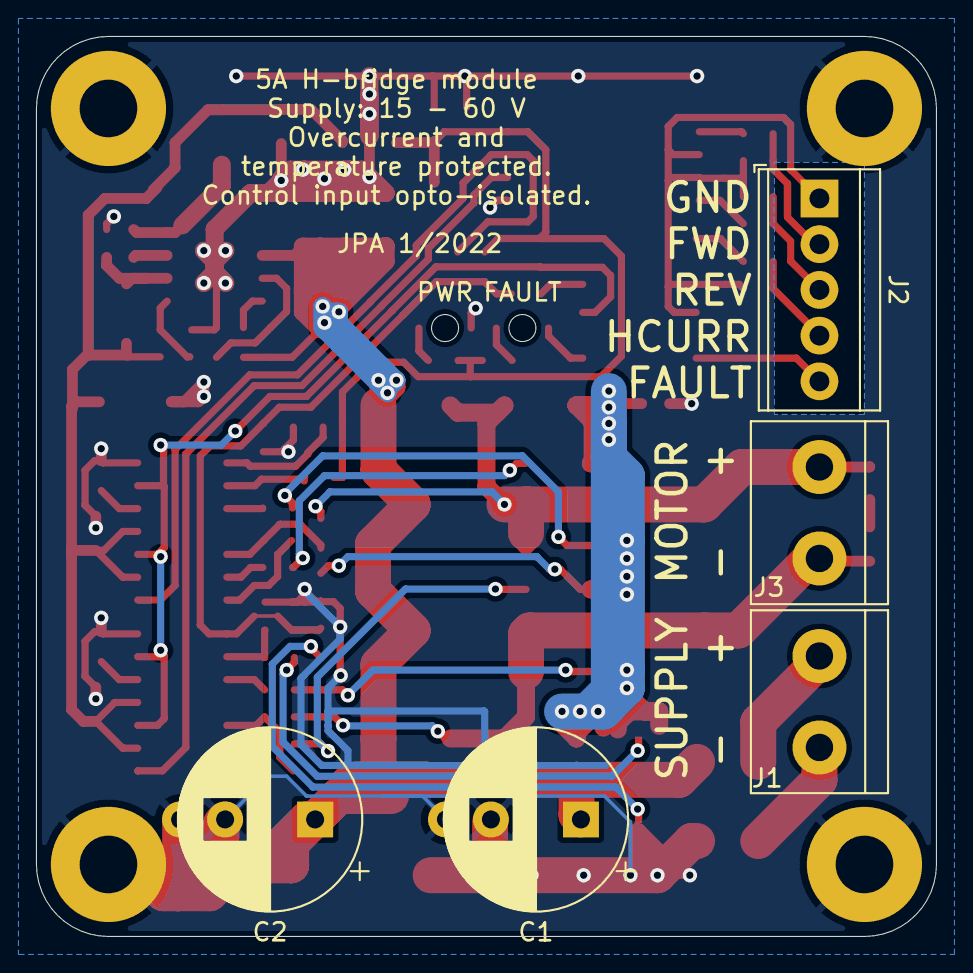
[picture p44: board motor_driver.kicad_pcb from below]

Board: 2 copper layers, 50.0 x 50.0 mm, 87 parts (5 on the bottom side), 51 nets.

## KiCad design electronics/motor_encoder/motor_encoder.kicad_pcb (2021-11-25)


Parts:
C1, C3: 10µF; C_0603_1608Metric
C2, C4: 100nF; C_0603_1608Metric
D1, D3: BAT54W; D_SOD-123
D2: STATUS; LED_0805_2012Metric
J1: Program; PinHeader_1x06_P2.54mm_Vertical
J2: Output; PinHeader_1x06_P2.54mm_Horizontal
L1: Ferrite 1k; L_0603_1608Metric
R1: 4k7; R_0603_1608Metric
R2, R3, R4: 100k; R_0603_1608Metric
R5, R6, R7: 100; R_0603_1608Metric
U1: AS5134; SSOP-20_5.3x7.2mm_P0.65mm

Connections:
+5V: C3.1, C4.1, D1.2 (A), J1.2, L1.2, U1.7 (VDD)
/A: J2.4, R5.1
/B: J2.3, R6.1
/CLK: J1.5, R3.1, U1.9 (DDCLK)
/CS: J1.6, R4.1, U1.4 (CS)
/DIO: J1.4, R2.1, U1.10 (DIO)
/VPP: C1.1, C2.1, D1.1 (K), J1.1, U1.1 (Prog)
/Z: J2.5, R7.1
GND: C1.2, C2.2, C3.2, C4.2, D2.1 (K), J1.3, J2.2, J2.6, R2.2, R3.2, R4.2, U1.2 (VSS), U1.5 (C2)
unnamed: D2.2 (A), R1.1
unnamed: D3.1 (K), L1.1
unnamed: D3.2 (A), J2.1
unnamed: R1.2, R5.2, U1.14 (A)
unnamed: R6.2, U1.15 (B)
unnamed: R7.2, U1.16 (Z)



Board: 2 copper layers, 30.0 x 30.0 mm, 18 parts (15 on the bottom side), 15 nets.

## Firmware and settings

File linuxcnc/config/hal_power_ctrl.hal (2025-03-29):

# Power-on and emergency stop control.

# Note: some components loaded here are used from other files.
loadrt not count=3
loadrt lut5 count=21
loadrt timedelay count=9
loadrt mux2 count=5
loadrt scale count=4
loadrt absmaxdecay count=1
loadrt abslimit count=1
loadrt sum2 count=4
loadrt spindle_load count=1
loadrt select8 count=1
loadrt edge count=2
loadrt pwmgen output_type=0,0
loadrt biquad count=1
loadrt median9 count=1
loadrt message names=msg_estop_btn,msg_estop_pause,msg_estop_motorx,msg_estop_motory,msg_estop_motorz messages="Emergency stop button pressed,Emergency stop by pause button during manual operation,Emergency stop due to X axis fault,Emergency stop due to Y axis fault,Emergency stop due to Z axis fault"

addf abslimit.0   servo-thread
addf absmaxdecay.0 servo-thread
addf scale.0    servo-thread
addf median9.0  servo-thread
addf biquad.0   servo-thread
addf spindle-load.0 servo-thread
addf scale.2    servo-thread
addf not.0      servo-thread
addf not.1      servo-thread
addf lut5.0     servo-thread
addf lut5.1     servo-thread
addf lut5.2     servo-thread
addf lut5.3     servo-thread
addf lut5.4     servo-thread
addf lut5.5     servo-thread
addf lut5.6     servo-thread
addf lut5.7     servo-thread
addf lut5.8     servo-thread
addf lut5.9     servo-thread
addf lut5.10    servo-thread
addf lut5.11    servo-thread
addf lut5.12    servo-thread
addf lut5.15    servo-thread
addf lut5.18    servo-thread
addf timedelay.0 servo-thread
addf timedelay.1 servo-thread
addf timedelay.2 servo-thread
addf timedelay.3 servo-thread
addf timedelay.4 servo-thread
addf timedelay.5 servo-thread
addf mux2.0     servo-thread
addf mux2.2     servo-thread
addf lut5.14    servo-thread
addf select8.0  servo-thread
addf lut5.19    servo-thread
addf lut5.20    servo-thread
addf lut5.17    servo-thread
addf timedelay.8 servo-thread
addf edge.0     servo-thread
addf edge.1     servo-thread
addf lut5.13    servo-thread
addf timedelay.6 servo-thread
addf timedelay.7 servo-thread
addf not.2      servo-thread
addf scale.3    servo-thread
addf pwmgen.update servo-thread
addf pwmgen.make-pulses servo-thread 
addf msg_estop_btn servo-thread
addf msg_estop_pause servo-thread
addf msg_estop_motorx servo-thread
addf msg_estop_motory servo-thread
addf msg_estop_motorz servo-thread

# Signals to hardware / simulator panel
newsig powerctl.mso1_switch bit
newsig powerctl.allow_auto bit
newsig powerctl.estop_btn bit
newsig powerctl.estop_off bit
newsig powerctl.estop_btn_with_power_good bit
newsig powerctl.run_btn bit
newsig powerctl.pause_btn bit
newsig powerctl.power_good bit
newsig powerctl.power_enable bit
newsig powerctl.program_paused bit
newsig powerctl.program_running bit
newsig powerctl.machine_homed bit
newsig powerctl.machine_is_on bit
newsig powerctl.start_homing_btn bit
newsig powerctl.pause_indicator bit
newsig powerctl.spindle_enable bit
newsig powerctl.spindle_at_speed bit
newsig powerctl.spindle_rpm float
newsig powerctl.spindle_rpm_fb float
newsig powerctl.spindle_rpm_fb_raw float
newsig powerctl.spindle_load float
newsig powerctl.spindle_load_filtered float
newsig powerctl.adaptive_feed float
newsig powerctl.velocity_mm_s float
newsig powerctl.velocity_mm_min float
newsig powerctl.ferror float
newsig powerctl.motor_ok bit
newsig powerctl.probe_sensor bit
newsig powerctl.probe_connected bit
newsig powerctl.paused_door_open bit
newsig powerctl.lift_z bit
newsig powerctl.coolant_on bit
newsig powerctl.coolant_auto bit
newsig powerctl.coolant_pulse bit
newsig powerctl.coolant_rate float
newsig powerctl.coolant_fluid bit
newsig powerctl.coolant_step bit
newsig powerctl.coolant_air bit
newsig powerctl.op_minute_counter bit
newsig powerctl.matrixkins_enable bit

newsig motordrive.0.runaway bit
newsig motordrive.1.runaway bit
newsig motordrive.2.runaway bit

net powerctl.program_paused <= halui.program.is-paused
net powerctl.program_running <= halui.program.is-running

net tool-prep-loop iocontrol.0.tool-prepare => iocontrol.0.tool-prepared
net tool-change-loop iocontrol.0.tool-change => iocontrol.0.tool-changed

# Messages for estop cause
net powerctl.estop_btn_with_power_good => msg_estop_btn.trigger
net powerctl.estop_pause => msg_estop_pause.trigger
net motordrive.0.runaway => msg_estop_motorx.trigger
net motordrive.1.runaway => msg_estop_motory.trigger
net motordrive.2.runaway => msg_estop_motorz.trigger

# Estop signal goes high when button is pressed or power
# is turned off. Post notification only on button press.
# lut5.18: in0 & in1
setp lut5.18.function 0x08
net powerctl.power_good => lut5.18.in-0
net powerctl.estop_btn => lut5.18.in-1
net powerctl.estop_btn_with_power_good <= lut5.18.out

#######################
# Run / pause buttons
# In automatic mode (MSO 1):
#  - Pressing RUN starts or resumes the program
#  - Pressing PAUSE pauses the program or acts as
#    emergency stop if program is not running.
#  - Opening door acts as pause
#  - Holding RUN overrides the door switch
#
# In setup mode (MSO 2):
#  - Automatic program start is not possible
#  - Pressing PAUSE acts as emergency stop
#  - Maximum speed 2000 mm/min (33 mm/s)
#  - Spindle cannot be started

# Actual emergency stop mechanism cuts power in hardware, but the software
# loop provides feedback for GUI and faster stopping.
# lut5.0: Combine estop signals (high = estop activated)
# out = !(in0 | in1 | in2 | in3 | in4)
setp lut5.0.function 0x01
net powerctl.estop_off lut5.0.out => iocontrol.0.emc-enable-in
net powerctl.estop_btn => lut5.0.in-0
net motordrive.fault => lut5.0.in-2

# lut5.1: If program is not running and door is closed, run button starts.
# out = in0 & in1 & in2 & in3 & in4
setp lut5.1.function 0x80000000
net powerctl.run_btn => lut5.1.in-0
net powerctl.program_idle halui.program.is-idle => lut5.1.in-1
net powerctl.machine_homed => lut5.1.in-2
net powerctl.power_good => lut5.1.in-3
net powerctl.mso1_switch => lut5.1.in-4
net powerctl.run lut5.1.out => halui.program.run

# lut5.2: If program is paused, run button resumes.
# out = in0 & in1 & in3
setp lut5.2.function 0x80
net powerctl.run_btn => lut5.2.in-0
net powerctl.program_paused halui.program.is-paused => lut5.2.in-1
net powerctl.allow_auto => lut5.2.in-2
net powerctl.resume lut5.2.out => halui.program.resume

# lut5.3: Pause with button, prevent running if not in MSO1 mode
# out = (in0 & in1) | (!in2 & in1)
setp lut5.3.function 0x8C
net powerctl.pause_btn => lut5.3.in-0
net powerctl.program_running => lut5.3.in-1
net powerctl.allow_auto => lut5.3.in-2
net powerctl.pause lut5.3.out => halui.program.pause

# lut5.14: Show notification if automatic movements are attempted with door open
# out = in0 & !in1
setp lut5.14.function 0x02
net powerctl.program_paused => lut5.14.in-0
net powerctl.allow_auto => lut5.14.in-1
net powerctl.paused_door_open <= lut5.14.out

# Jogging / homing cannot be paused, so if program is not
# running, pause button should act as estop.
# lut5.4: Set estop when program not running and pause pressed
# out = (in0 & in1)
setp lut5.4.function 0x08
net powerctl.pause_btn => lut5.4.in-0
net powerctl.program_idle halui.program.is-idle => lut5.4.in-1
net powerctl.estop_pause lut5.4.out => lut5.0.in-1

# Override MSO1 switch & door switch state when RUN button is held down.
# This allows ISO16090 MSO3 "manual intervention" to keep running
# with guards open. As soon as the RUN button is released the program
# will be paused.
# out = in0 | in1
setp timedelay.3.on-delay 0.2
setp timedelay.3.off-delay 0.01
setp lut5.5.function 0x0E
net powerctl.run_btn => timedelay.3.in
net powerctl.run_btn_held timedelay.3.out => lut5.5.in-0
net powerctl.mso1_switch => lut5.5.in-1
net powerctl.allow_auto <= lut5.5.out

# Hardware power enable after e-stop is off
# Power is turned on in three conditions:
#  1. Hardware power switch is turned on (falling edge on estop_btn)
#  2. Hardware e-stop switch is turned off (falling edge on estop_btn)
#  3. User interface power button is pressed (halui.machine.is-on high state)
# Power is turned off when:
#  1. Either hardware or software estop (low state on estop_off)
#  2. User interface power button is pressed (halui.machine.is-on falling edge)
#
net powerctl.estop_btn => edge.0.in
net powerctl.machine_is_on => edge.1.in

setp timedelay.7.on-delay 0.1
setp timedelay.7.off-delay 0.1
net powerctl.estop_btn => timedelay.7.in

# lut5.13:
# out = 0 when !in4 || in1
# out = 1 when  in4 & (!in2 || in3)
# out = in0 otherwise
setp lut5.13.function 0x32230000
net powerctl.estop_off => lut5.13.in-4
net powerctl.ui_power_off edge.1.out => lut5.13.in-1
net powerctl.estop_btn_delayed timedelay.7.out => lut5.13.in-2
net powerctl.machine_is_on => lut5.13.in-3
net powerctl.power_enable_raw lut5.13.out => lut5.13.in-0

# Power-enable needs a bit of on-delay to avoid partial resets due to short estop press
setp timedelay.6.on-delay 1
setp timedelay.6.off-delay 0.01
net powerctl.power_enable_raw => timedelay.6.in
net powerctl.power_enable <= timedelay.6.out
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

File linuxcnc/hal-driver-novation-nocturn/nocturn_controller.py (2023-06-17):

#!/usr/bin/env python2

'''Using Novation Nocturn as LinuxCNC jog controller.

The hardware communication side is in nocturn_midi.py.
This file implements the controller logic and ties to LinuxCNC HAL.

Instead of exposing a set of pins and connecting them, this
script takes the lazy approach and just uses setp to write
e.g. halui.axis.x.increment-plus directly.
'''

import hal
import linuxcnc
import time
import nocturn_midi
import traceback

def delay():
    '''Delay to let LinuxCNC GUI notice action'''
    time.sleep(0.05)

class JogSpeed:
    '''Control jog speed and increment based on slider position'''
    increment = 'jog_increment'
    speed = 'jog_speed'
        
    def __init__(self, comp):
        self.comp = comp
        self.comp.newpin(self.increment, hal.HAL_FLOAT, hal.HAL_OUT)
        self.comp.newpin(self.speed, hal.HAL_FLOAT, hal.HAL_OUT)

        # Default settings in case we don't get initial slider position from the hardware
        self.comp[self.increment] = 1.0
        self.comp[self.speed] = 1000
    
    def __call__(self, event):
        pos = round(event[1] * 3)
        if pos == 0:
            step, speed = 10, 2000
        elif pos == 1:
            step, speed = 1, 1000
        elif pos == 2:
            step, speed = 0.1, 100
        elif pos == 3:
            step, speed = 0.01, 10
        
        self.comp[self.increment] = step
        self.comp[self.speed] = speed

class JogMotion:
    '''Jog single axis with an encoder'''

    def __init__(self, comp, axis):
        self.comp = comp
        self.counts = "jog_%s_counts" % axis
        self.comp.newpin(self.counts, hal.HAL_S32, hal.HAL_OUT)

    def __call__(self, event):
        if self.comp['machine-is-on'] == 0:
            return
        
        if self.comp['jog_enabled'] == 0 or self.comp['machine-homed'] == 0:
            return
    
        self.comp[self.counts] += event[1]

class AutoZeroEncoder:
    '''Encoder that resets value when machine is powered off'''
    def __init__(self, comp, pinname):
        self.comp = comp
        self.pinname = pinname
        self.comp.newpin(self.pinname, hal.HAL_S32, hal.HAL_OUT)
    
    def __call__(self, event):
        if self.comp['machine-is-on'] == 0:
            self.comp[self.pinname] = 0
        elif event[0] != 'poll':
            self.comp[self.pinname] += event[1]

class Button:
    '''Button press to HAL pin'''
    def __init__(self, comp, pinname):
        self.comp = comp
        self.pinname = pinname
        self.comp.newpin(self.pinname, hal.HAL_BIT, hal.HAL_OUT)
    
    def __call__(self, event):
        if self.comp['machine-is-on'] == 0 or self.comp['machine-homed'] == 0:
            event[1] = 0

        self.comp[self.pinname] = event[1]

class ToggleButton:
    '''Toggle HAL pin on every press'''
    def __init__(self, comp, pinname, default = False):
        self.comp = comp
        self.pinname = pinname
        self.comp.newpin(self.pinname, hal.HAL_BIT, hal.HAL_OUT)
        self.comp[self.pinname] = default
    
    def __call__(self, event):
        if self.comp['machine-is-on'] == 0:
            self.comp[self.pinname] = False
        elif event[1]:
            self.comp[self.pinname] = not self.comp[self.pinname]

class MDIButton:
    '''Button that runs MDI command'''
    def __init__(self, comp, mdi_command):
        self.comp = comp
        self.mdi_command = mdi_command
    
    def __call__(self, event):
        if event[1] and self.comp['machine-is-on'] and self.comp['machine-homed']:
            cmd = linuxcnc.command()
            cmd.mode(linuxcnc.MODE_MDI)
            cmd.wait_complete()
            cmd.mdi(self.mdi_command)

class Pulse:
    '''Give pulse on a pin'''
    def __init__(self, comp, pinname):
        self.comp = comp
        self.pinname = pinname
        try:
            self.comp.newpin(self.pinname, hal.HAL_BIT, hal.HAL_OUT)
        except ValueError:
            pass # Duplicate pin
    
    def __call__(self, event):
        if event[0] == 'poll':
            self.comp[self.pinname] = 0
        else:
            self.comp[self.pinname] = 1

class Led:
    '''Polling HAL pin to LED state'''
    def __init__(self, comp, hw, pinname, led_idx, blink_time = 0.0, invert = False):
        self.comp = comp
        self.hw = hw
        self.pinname = pinname
        self.led_idx = led_idx
        self.blink_time = blink_time
        self.invert = invert
        self.prev_state = None
        try:
            self.comp.newpin(self.pinname, hal.HAL_BIT, hal.HAL_IN)
        except ValueError:
            pass # Duplicate pin
    
    def __call__(self, event):
        if self.comp[self.pinname] ^ self.invert:
            if self.blink_time > 0:
                state = ((time.time() % self.blink_time) < (self.blink_time / 2.0))
            else:
                state = True
        else:
            state = False
        
        if self.comp['machine-is-on'] == 0 or self.comp['machine-homed'] == 0:
            state = False

        if self.hw.midi_port_idx is None:
            self.prev_state = None
        elif state != self.prev_state:
            self.prev_state = state
            self.hw.set_button_led(self.led_idx, state)

class RelativeZeroLed:
    '''Light led if relative coordinate is zero'''
    def __init__(self, comp, hw, pinname, led_idx):
        self.comp = comp
        self.hw = hw
        self.pinname = pinname
        self.led_idx = led_idx
        self.prev_state = None
        self.comp.newpin(self.pinname, hal.HAL_FLOAT, hal.HAL_IN)
    
    def __call__(self, event):
        state = abs(self.comp[self.pinname]) <= 0.01

        if self.comp['machine-is-on'] == 0:
            state = False
        
        if self.comp['program-idle'] == 0 or self.comp['machine-homed'] == 0:
            state = False

        if self.hw.midi_port_idx is None:
            self.prev_state = None
        elif state != self.prev_state:
            self.prev_state = state
            self.hw.set_button_led(self.led_idx, state)
        

class EncoderRing:
    '''Show current value on encoder led ring as a filled scale'''
    def __init__(self, comp, hw, pinname, enc_idx, minval = 0.0, maxval = 1.0, ledmode = 2, wrap = False):
        self.comp = comp
        self.hw = hw
        self.pinname = pinname
        self.enc_idx = enc_idx
        self.minval = minval
        self.maxval = maxval
        self.ledmode = ledmode
        self.wrap = wrap
        self.comp.newpin(self.pinname, hal.HAL_FLOAT, hal.HAL_IN)
    
    def __call__(self, event):
        if self.comp['machine-is-on'] == 0:
            self.hw.set_encoder_leds(self.enc_idx, 0, 0)
        else:
            v = (self.comp[self.pinname] - self.minval) / (self.maxval - self.minval)
            if self.wrap: v = v % 1.0
            self.hw.set_encoder_leds(self.enc_idx, self.ledmode, v)

class NocturnController:
    def __init__(self):
        self.comp = hal.component("nocturn")
        self.comp.newpin('machine-is-on', hal.HAL_BIT, hal.HAL_IN)
        self.comp.newpin('program-idle', hal.HAL_BIT, hal.HAL_IN)
        self.comp.newpin('machine-homed', hal.HAL_BIT, hal.HAL_IN)
        self.comp.newpin('jog_enabled', hal.HAL_BIT, hal.HAL_IN)
        
        self.hw = nocturn_midi.NocturnMidi()
        self.handlers = {
            'slider00': JogSpeed(self.comp),
            'enc08': AutoZeroEncoder(self.comp, 'x_offset'),
            'enc07': AutoZeroEncoder(self.comp, 'y_offset'),
            'enc06': AutoZeroEncoder(self.comp, 'z_offset'),
            'enc05': AutoZeroEncoder(self.comp, 'spindle_override'),
            'enc04': AutoZeroEncoder(self.comp, 'feed_override'),
            'enc03': [JogMotion(self.comp, 'x'),     Pulse(self.comp, "start_jog")],
            'enc02': [JogMotion(self.comp, 'y'),     Pulse(self.comp, "start_jog")],
            'enc01': [JogMotion(self.comp, 'z'),     Pulse(self.comp, "start_jog")],
            'enc00': [JogMotion(self.comp, 'a'),     Pulse(self.comp, "start_jog")],
            'btn03': [Button(self.comp, "x_minus"),  Pulse(self.comp, "start_jog")],
            'btn11': [Button(self.comp, "x_plus"),   Pulse(self.comp, "start_jog")],
            'btn02': [Button(self.comp, "y_minus"),  Pulse(self.comp, "start_jog")],
            'btn10': [Button(self.comp, "y_plus"),   Pulse(self.comp, "start_jog")],
            'btn01': [Button(self.comp, "z_minus"),  Pulse(self.comp, "start_jog")],
            'btn09': [Button(self.comp, "z_plus"),   Pulse(self.comp, "start_jog")],
            'btn00': [Button(self.comp, "a_minus"),  Pulse(self.comp, "start_jog")],
            'btn08': [Button(self.comp, "a_plus"),   Pulse(self.comp, "start_jog")],
            'btn07': ToggleButton(self.comp, "clear_offsets", default = True),
            'btn06': ToggleButton(self.comp, "lift_z"),
            'btn15': MDIButton(self.comp, 'G10 L20 P0 X0'),
            'btn14': MDIButton(self.comp, 'G10 L20 P0 Y0'),
            'btn13': MDIButton(self.comp, 'G10 L20 P0 Z0'),
            'btn12': MDIButton(self.comp, 'o<z_probe_pad> call'),
            'btn05': MDIButton(self.comp, 'o<tool_change_pos> call'),
            'btn04': MDIButton(self.comp, 'o<tool_length_probe> call'),
            'poll': [
                Pulse(self.comp, "start_jog"),
                Led(self.comp, self.hw, 'program-idle', 0),
                Led(self.comp, self.hw, 'program-idle', 1),
                Led(self.comp, self.hw, 'program-idle', 2),
                Led(self.comp, self.hw, 'program-idle', 3),
                Led(self.comp, self.hw, 'program-idle', 8),
                Led(self.comp, self.hw, 'program-idle', 9),
                Led(self.comp, self.hw, 'program-idle', 10),
                Led(self.comp, self.hw, 'program-idle', 11),
                Led(self.comp, self.hw, 'clear_offsets', 7, invert = True),
                Led(self.comp, self.hw, 'lift_z', 6),
                EncoderRing(self.comp, self.hw, 'led_x_offset', 8, 0.0, 1.0, 4, True),
                EncoderRing(self.comp, self.hw, 'led_y_offset', 7, 0.0, 1.0, 4, True),
                EncoderRing(self.comp, self.hw, 'led_z_offset', 6, 0.0, 1.0, 4, True),
                EncoderRing(self.comp, self.hw, 'led_spindle_override', 5, 0.0, 2.0, 0),
                EncoderRing(self.comp, self.hw, 'led_feed_override', 4, 0.0, 2.0, 0),
                RelativeZeroLed(self.comp, self.hw, 'rel_x', 15),
                RelativeZeroLed(self.comp, self.hw, 'rel_y', 14),
                RelativeZeroLed(self.comp, self.hw, 'rel_z', 13),
            ]
        }

        self.handlers['poll'] += [
            self.handlers['enc08'],
            self.handlers['enc07'],
            self.handlers['enc06'],
            self.handlers['enc05'],
            self.handlers['enc04'],
        ]
        
        self.comp.ready()

    def poll(self):
        try:
            event = self.hw.parse_inputs()
            if event:
                self.handle_event(event)
            else:
                time.sleep(0.05)
                self.handle_event(('poll', None))
                self.hw.check_midi_connection()
        except KeyboardInterrupt:
            raise
        except:
            traceback.print_exc()

    def handle_event(self, event):
        if event[0] in self.handlers:
            handlers = self.handlers[event[0]]
            
            if isinstance(handlers, list):
                for handler in handlers:
                    handler(event)
            else:
                handlers(event)
    
if __name__ == '__main__':
    try:
        nocturn = NocturnController()
        while True:
            nocturn.poll()
    except KeyboardInterrupt:
        nocturn.hw.leds_off()
        raise SystemExit

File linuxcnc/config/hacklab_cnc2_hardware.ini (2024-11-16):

# Use this file for starting LinuxCNC with actual hardware.

[EMC]
VERSION = 1.1
MACHINE = HacklabCNC2
DEBUG = 0

[HOSTMOT2]
DRIVER=hm2_pci
BOARD=5i25
CONFIG="num_encoders=4 num_pwmgens=4 num_stepgens=0"

[ENCODERS]
STEP_PER_MM_X = 200
STEP_PER_MM_Y = 200
STEP_PER_MM_Z = 600

[MOTORDRIVE]
SUPPLY_VOLTAGE = 48

[HAL]
HALFILE = hal_core.hal
HALFILE = hal_power_ctrl.hal
HALFILE = hal_motor_pid.hal
HALFILE = hal_probe_cam.hal
HALFILE = hal_hostmot2.hal
HALFILE = hal_nocturn.hal
POSTGUI_HALFILE = hal_gladevcp.hal
HALUI = halui

#INCLUDE hacklab_cnc2_common.ini

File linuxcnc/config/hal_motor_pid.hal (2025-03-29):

# LinuxCNC HAL configuration for motor PID controllers.

# Module loading
loadrt pid num_chan=3
loadrt runawayprot count=3
loadrt logic names=logic.or3 personality=0x203
loadrt offset count=1
loadrt limit3 count=1
loadrt limit2 count=1
loadrt zmap count=1

addf offset.0.update-feedback              servo-thread 1
addf zmap.0                                servo-thread
addf offset.0.update-output                servo-thread

addf pid.0.do-pid-calcs                    servo-thread
addf pid.1.do-pid-calcs                    servo-thread
addf pid.2.do-pid-calcs                    servo-thread

addf runawayprot.0                         servo-thread
addf runawayprot.1                         servo-thread
addf runawayprot.2                         servo-thread
addf logic.or3                             servo-thread

addf mux2.3                                servo-thread
addf mux2.4                                servo-thread
addf sum2.3                                servo-thread
addf limit3.0                              servo-thread
addf limit2.0                              servo-thread

#########################
# Calibrated kinematics #
#########################

setp matrixkins.c0 [MATRIXKINS]C0
setp matrixkins.c1 [MATRIXKINS]C1
setp matrixkins.c2 [MATRIXKINS]C2
setp matrixkins.c3 [MATRIXKINS]C3
setp matrixkins.c4 [MATRIXKINS]C4
setp matrixkins.c5 [MATRIXKINS]C5
setp matrixkins.c6 [MATRIXKINS]C6
setp matrixkins.c7 [MATRIXKINS]C7
setp matrixkins.c8 [MATRIXKINS]C8
net powerctl.matrixkins_enable => matrixkins.enable

####################
# X axis / joint 0 #
####################

# Enable signal for the motor driver
newsig motordrive.0.enable bit
sets motordrive.0.enable FALSE
net motordrive.0.enable => pid.0.enable
net motordrive.0.enable <= joint.0.amp-enable-out 

# Feedback signal from encoder
newsig motordrive.0.feedback float
net motordrive.0.feedback => pid.0.feedback        # Feedback to PID control
net motordrive.0.feedback => joint.0.motor-pos-fb  # Feedback to GUI

# PWM output drive signal
newsig motordrive.0.control float
net motordrive.0.control <= pid.0.output

# Commanded position from motion controller
net motordrive.0.command joint.0.motor-pos-cmd => pid.0.command

# PID parameters from ini file
setp pid.0.Pgain [JOINT_0]P
setp pid.0.Igain [JOINT_0]I
setp pid.0.Dgain [JOINT_0]D
setp pid.0.bias [JOINT_0]BIAS
setp pid.0.FF0 [JOINT_0]FF0
setp pid.0.FF1 [JOINT_0]FF1
setp pid.0.FF2 [JOINT_0]FF2
setp pid.0.deadband [JOINT_0]DEADBAND
setp pid.0.maxoutput [JOINT_0]MAX_OUTPUT

# Monitoring PID feedback loop
setp runawayprot.0.control-threshold 12.0
setp runawayprot.0.feedback-threshold 0.01
setp runawayprot.0.time-threshold 0.2
net motordrive.0.feedback => runawayprot.0.feedback
net motordrive.0.control => runawayprot.0.control
net motordrive.0.runaway runawayprot.0.out => logic.or3.in-00

####################
# Y axis / joint 1 #
####################

# Enable signal for the motor driver
newsig motordrive.1.enable bit
sets motordrive.1.enable FALSE
net motordrive.1.enable => pid.1.enable
net motordrive.1.enable <= joint.1.amp-enable-out 

# Feedback signal from encoder
newsig motordrive.1.feedback float
net motordrive.1.feedback => pid.1.feedback        # Feedback to PID control
net motordrive.1.feedback => joint.1.motor-pos-fb  # Feedback to GUI

# PWM output drive signal
newsig motordrive.1.control float
net motordrive.1.control <= pid.1.output

# Commanded position from motion controller
net motordrive.1.command joint.1.motor-pos-cmd => pid.1.command

# PID parameters from ini file
setp pid.1.Pgain [JOINT_1]P
setp pid.1.Igain [JOINT_1]I
setp pid.1.Dgain [JOINT_1]D
setp pid.1.bias [JOINT_1]BIAS
setp pid.1.FF0 [JOINT_1]FF0
setp pid.1.FF1 [JOINT_1]FF1
setp pid.1.FF2 [JOINT_1]FF2
setp pid.1.deadband [JOINT_1]DEADBAND
setp pid.1.maxoutput [JOINT_1]MAX_OUTPUT

# Monitoring PID feedback loop
setp runawayprot.1.control-threshold 12.0
setp runawayprot.1.feedback-threshold 0.01
setp runawayprot.1.time-threshold 0.2
net motordrive.1.feedback => runawayprot.1.feedback
net motordrive.1.control => runawayprot.1.control
net motordrive.1.runaway runawayprot.1.out => logic.or3.in-01

####################
# Z axis / joint 2 #
####################

# Enable signal for the motor driver
newsig motordrive.2.enable bit
sets motordrive.2.enable FALSE
net motordrive.2.enable => pid.2.enable
net motordrive.2.enable <= joint.2.amp-enable-out 

# Feedback signal from encoder
newsig motordrive.2.feedback float
net motordrive.2.feedback => pid.2.feedback        # Feedback to PID control
net motordrive.2.feedback => offset.0.fb-in  # Feedback to GUI
net motordrive.2.offset_fb offset.0.fb-out => joint.2.motor-pos-fb

# PWM output drive signal
newsig motordrive.2.control float
net motordrive.2.control <= pid.2.output

# Commanded position from motion controller
net motordrive.2.offset_cmd joint.2.motor-pos-cmd => offset.0.in
net motordrive.2.command offset.0.out => pid.2.command

# PID parameters from ini file
setp pid.2.Pgain [JOINT_2]P
setp pid.2.Igain [JOINT_2]I
setp pid.2.Dgain [JOINT_2]D
setp pid.2.bias [JOINT_2]BIAS
setp pid.2.FF0 [JOINT_2]FF0
setp pid.2.FF1 [JOINT_2]FF1
setp pid.2.FF2 [JOINT_2]FF2
setp pid.2.deadband [JOINT_2]DEADBAND
setp pid.2.maxoutput [JOINT_2]MAX_OUTPUT

# Monitoring PID feedback loop
setp runawayprot.2.control-threshold 20.0
setp runawayprot.2.feedback-threshold 0.01
setp runawayprot.2.time-threshold 0.2
net motordrive.2.feedback => runawayprot.2.feedback
net motordrive.2.control => runawayprot.2.control
net motordrive.2.runaway runawayprot.2.out => logic.or3.in-02

# Combined OR of all fault signals
net motordrive.fault <= logic.or3.or

#################
# Z axis offset #
#################

setp zmap.0.reset 1

net machine.pos_x axis.x.pos-cmd => zmap.0.x
net machine.pos_y axis.y.pos-cmd => zmap.0.y
net machine.rel_z => zmap.0.probe-z
net powerctl.probe_sensor => zmap.0.probe

# Select either zmap or +100mm offset for Z axis.
# This can be used for e.g. tool changing or for dry run
net powerctl.lift_z => mux2.3.sel
net powerctl.zmap zmap.0.z => mux2.3.in0
setp mux2.3.in1 100

# Calculate maximum offset to not exceed Z axis maximum
net motordrive.2.cmd_abs axis.z.pos-cmd => sum2.3.in0
setp sum2.3.gain0 -1.0
setp sum2.3.offset [AXIS_Z]MAX_LIMIT

# Limit velocity and maximum value
setp limit3.0.maxv 10
setp limit3.0.maxa 50
setp limit3.0.smooth-steps 100
net motordrive.2.offset-req2 mux2.4.out => limit3.0.in
net motordrive.2.offset-limv limit3.0.out => limit2.0.in
net motordrive.2.max-offset sum2.3.out => limit2.0.max
net motordrive.2.offset limit2.0.out => offset.0.offset

# Don't move when door is open
net motordrive.2.offset-limv => mux2.4.in0
net motordrive.2.offset-req mux2.3.out => mux2.4.in1
net powerctl.allow_auto => mux2.4.sel

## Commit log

2021-11-25 Add preliminary wiring diagram and parts list
    [sergei2-wiring.kicad_sch]
2021-11-25 Add customized pinout and bitfile for Mesa 6i25 card
    [sergei2-wiring.kicad_sch]
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2022-01-01 Fix FPGA pin mapping
    Mesa 6i25 IO numbers do not directly map to DB25 pin numbers.
2022-01-15 Update motor driver and power control PCB designs
    [motor_driver.kicad_pcb, motor_driver.kicad_sch, motor_driver.sch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]
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2022-03-14 Update wiring diagram & motor driver part values
    [motor_driver.kicad_pcb, motor_driver.kicad_sch, power_control_pcb.kicad_pcb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]
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2022-04-21 Add PID tune panel
    [pid_tune.hal]
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2022-04-23 Camera holder 3D model
    [camera_holder.stl]
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2022-04-27 LinuxCNC config: add interface to hardware buttons
    [hacklab_cnc2_common.ini, hacklab_cnc2_hardware.ini, hacklab_cnc2_simulation.ini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]
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2022-05-07 Add PWM output for spindle control
    [sergei2-wiring.kicad_sch]
2022-05-07 Fix Y axis direction
    [hacklab_cnc2_common.ini, hal_hostmot2.hal]
2022-05-13 LinuxCNC config for spindle control
    [hacklab_cnc2_common.ini, hacklab_cnc2_hardware.ini, hacklab_cnc2_simulation.ini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]
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2022-06-03 GUI and USB control functions
    [hacklab_cnc2_hardware.ini, hacklab_cnc2_simulation.ini, hal_gladevcp.hal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]
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2022-06-06 Add motor runaway protection
    [hal_motor_pid.hal, hal_power_ctrl.hal]
2022-06-11 Use FSESC 4.20 for driving Z axis, add brake shunt
    [braking_shunt.kicad_pcb, braking_shunt.kicad_sch, sergei2-wiring.kicad_sch]
2022-06-11 HAL config and PID tuning for FSESC driver
    [hacklab_cnc2_common.ini, hal_hostmot2.hal, hal_motor_pid.hal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]
2022-06-11 Add filter for spindle-at-speed signal
    [hal_hostmot2.hal, hal_power_ctrl.hal]
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2022-06-17 Import probescreen code from https://github.com/linuxcnc-probe-screen/probe-screen-ng
    [hacklab_cnc2_common.ini, install_add_to_your.ini, install_del_from_your.hal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]
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2022-06-18 Camera retry and offset
    [hacklab_cnc2_common.ini]
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2022-06-25 Small config fixes
    [hal_power_ctrl.hal]
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2022-07-22 Add matrixkins for calibration
    [hacklab_cnc2_common.ini, hal_motor_pid.hal]
2022-07-22 Nocturn USB controller button layout
    [hacklab_cnc2_common.ini, hacklab_cnc2_hardware.ini, hacklab_cnc2_simulation.ini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]
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2022-07-26 Fix some jitter with hold-to-run with door open
    [hal_power_ctrl.hal]
2022-07-31 Timeout preview in AXIS
    [hacklab_cnc2_common.ini]
2022-08-03 Switch to custom probe screen
    [hacklab_cnc2_common.ini, hal_power_ctrl.hal, hal_simulator.hal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]
2022-08-05 Add probe type selection
    [hal_gladevcp.hal]
2022-08-06 Probing fixes
    [hacklab_cnc2_common.ini, hal_power_ctrl.hal]
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2022-08-06 Include angle in probe results
    [hacklab_cnc2_common.ini]
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2022-08-06 Config fixes
    [hacklab_cnc2_common.ini]
2022-09-22 Improve coordinate system handling, add selector buttons to sidebar
    [hacklab_cnc2_common.ini]
2022-09-24 Add FreeCAD tool library
    [ballend.fcstd, bullnose.fcstd, chamfer.fcstd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]
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2022-09-24 Fix #10
    [hal_power_ctrl.hal, toe_clamp.FCStd]
2022-09-24 Disable M6 remap, fixes #15
    The remap wasn't really working anyway.
    Related: https://github.com/LinuxCNC/linuxcnc/issues/246
    [hacklab_cnc2_common.ini]
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2022-10-23 Update parts list and wiring diagram
    [sergei2-wiring.kicad_sch]
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2022-11-11 GUI controls for coolant pump
    [hacklab_cnc2_hardware.ini, hal_gladevcp.hal, hal_hostmot2.hal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]
2022-11-11 Limit acceleration when using lift Z button
    [hal_motor_pid.hal]
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2022-11-12 FPGA firmware: add coolant pump PWM (fix prev. commit)
2022-11-12 Coolant pump PWM config
    [hal_hostmot2.hal, hal_power_ctrl.hal]
2022-11-18 Simplify spindle monitoring, avoid false errors
    [hal_power_ctrl.hal]
2022-11-18 Fix coolant auto functionality
    [hal_power_ctrl.hal]
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2022-12-10 Workaround problems with Z axis driver
    [hacklab_cnc2_common.ini, hal_nocturn.hal]
2022-12-16 Update probe port in wiring diagram.
    Switching to 3.5mm jack to provide power to 3D probe.
    [sergei2-wiring.kicad_sch]
2023-01-07 Updated Z motor driver settings
    [hacklab_cnc2_common.ini, hal_hostmot2.hal, hal_motor_pid.hal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]
2023-01-07 Less aggressive Z PID
    [hacklab_cnc2_common.ini]
2023-01-07 Reduce Z jog acceleration back
    [hal_nocturn.hal]
2023-01-07 Add delay to power_enable after estop
    [hal_hostmot2.hal, hal_power_ctrl.hal]
2023-01-15 Add debounce filtering to button inputs
    Fixes some EMI issues where VFD causes spurious pulses
    to lines that rely on pull-up resistor.
    [hal_hostmot2.hal]
2023-01-15 Remove Z coordinate from camera tab
    [qtvcp_cameratab.hal]
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2023-01-23 Show informative messages in sidebar
    [hacklab_cnc2_common.ini, hal_power_ctrl.hal]
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2023-01-30 Improvements for lift_z functionality
    - Pause when door open
    - Workaround Z max limit not working (LinuxCNC/linuxcnc#2316)
    - Add notification to sidebar
    [hal_motor_pid.hal, hal_power_ctrl.hal]
2023-01-30 Dont start spindle when probe connected
    [hal_hostmot2.hal, hal_power_ctrl.hal, sergei2-wiring.kicad_sch]
2023-01-31 Better estop/power logic
    Re-enable power only by manual action after e-stop.
    This way any fault state results in hardware power-off
    until user checks things out.
    [hal_power_ctrl.hal]
2023-02-04 Power control fixes
    [hal_power_ctrl.hal]
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2023-02-11 Cooland fluid pump settings
    [hal_hostmot2.hal, hal_power_ctrl.hal]
2023-02-12 Buck regulator errata
    [buck_regulator.kicad_sch]
2023-03-26 Update offset for new camera
    Also added way to set the optical center of the camera
    (as aligned with the machine Z axis).
    This allows precise measurements at any height.
    [hacklab_cnc2_common.ini, hal_probe_cam.hal, qtvcp_cameratab.hal]
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2023-05-20 Adjust fluid pump PWM
    [hal_hostmot2.hal]
2023-06-17 Nocturn: Small fixes
    - Fix LED behavior in corner cases
    - Avoid GUI warnings if button is pressed too soon
    [nocturn_controller.py]
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2024-02-03 Fix coolant pump activation when air is in pulse mode
    [hal_hostmot2.hal, hal_power_ctrl.hal]
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2024-04-06 Z offset fixes
    [hal_motor_pid.hal]
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2024-06-18 Increase X axis runawayprot threshold, seem to get false triggers
    [hal_motor_pid.hal]
2024-08-17 Adjust runawayprot thresholds
    X-axis was getting spurious triggers when matrixkins moves it very slowly.
    [hal_motor_pid.hal]
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2024-11-02 Set matrixkins Z calibration based on bed, not spindle.
    This is more useful in practice.
    [hacklab_cnc2_common.ini]
2024-11-14 Add spindle speed sensor & extra fan (#11, #20)
    This should allow monitoring the spindle load level and
    to cool it better at low RPM.
    [sergei2-wiring.kicad_sch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]
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2024-11-16 FPGA pinout fix
    Encoder 3, not 0
    [hal_hostmot2.hal]
2024-11-16 Fix FPGA pinout
    Encoder input seems to require both pins defined.
2024-11-16 Spindle load measurement bugfixes
    [hacklab_cnc2_common.ini, hacklab_cnc2_hardware.ini, hal_gladevcp.hal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]
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2025-01-04 Recalibration after Z mounting plate replacement
    [hacklab_cnc2_common.ini, hal_motor_pid.hal, z_carriage_mount.FCStd]
2025-01-18 Increase PID deadband to stop vibrations when idle
    [hacklab_cnc2_common.ini]
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2025-02-01 Updated spindle magnet mount
    Spindle speed sensor now uses OH137 hall sensor.
    Fixes #23
    [spindle_fan_magnetmount.FCStd]
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2025-07-19 FPGA: Use IO19 in place of broken IO28
    Got a voltage spike when hotplugging stuff
    and broke the IO pin on 6i25.
2025-07-24 Spindle fan: Add holder for Electrolux EF150 filters
    Should be more effective and easier to clean than the previous filter.
    [spindle_fan-IntakeFilterEF150Holder.stl]
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
